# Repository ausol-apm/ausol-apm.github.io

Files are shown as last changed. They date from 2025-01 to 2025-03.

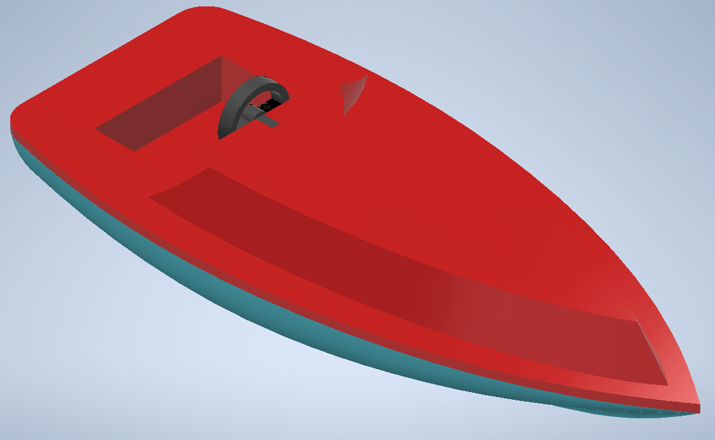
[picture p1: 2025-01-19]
Design and simulation/Inventor/Modelado juguetes/Imagenes juguetes/Barco.png

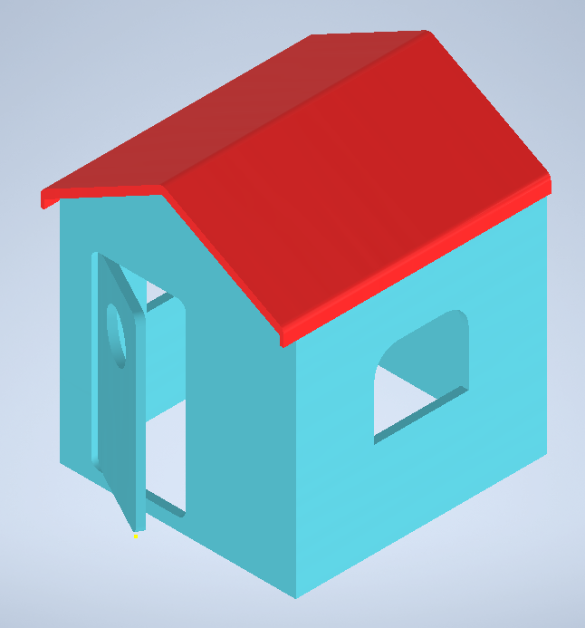
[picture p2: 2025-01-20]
Design and simulation/Inventor/Modelado juguetes/Imagenes juguetes/Casa.png

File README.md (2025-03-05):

**AUTOMATION SOLUTIONS - AUSOL**  
Propuesta de automatización de linea de producción de 3 juguetes, para la empresa _Bricajo Toys_.

**Integrantes**  
- Yovany Esneider Vargas Gutierrez
- Brian Enrique Muñoz Garcia
- Joyner Stiven Caballero Abril
- Camilo Andres Apraez Zamora

Se optó por montar la página web en Google Sites, para acceder a ella dirigirse a [Ausol Site](https://sites.google.com/unal.edu.co/ausol-automation-solutions).  
El video resumen se encuentra en la plataforma de YouTube [Video Resumen](https://youtu.be/QcR64jWf5vM).

*Automatización de Procesos de Manufactura  
Universidad Nacional de Colombia  
Sede Bogotá  
2024-2S*

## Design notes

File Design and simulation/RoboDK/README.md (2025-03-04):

Debido a inconvenientes con el tamaño del archivo .rdk, no fue posible subirlo directamente al GitHub. Por esta razón, se proporciona un enlace de Google Drive para su descarga.
https://drive.google.com/file/d/1TmyBnXiAjbIdtEMR1A-sOKN9FEcNRLlI/view?usp=sharing

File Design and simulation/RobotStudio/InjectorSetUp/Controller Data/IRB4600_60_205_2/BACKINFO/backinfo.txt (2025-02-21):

>>SYSTEM_ID:
VIRTUAL_USE

>>PRODUCTS_ID:
RobotWare Version: 6.15.08.00

  RobotWare Base
  English
  Drive System IRB 460/640/660/760/4600/66xx/6700
  ADU-790A in position X3
  ADU-790A in position Y3
  ADU-790A in position Z3
  Axis Calibration
  IRB 4600-60/2.05 Type C

>>HOME:
All public files and directories

>>SYSPAR:
SYS.cfg
PROC.cfg
MMC.cfg
EIO.cfg
SIO.cfg
MOC.cfg

>>TASK1: (T_ROB1,,)
SYSMOD\user.sys @ 
PROGMOD\Module1.mod @ 
PROGMOD\CalibData.mod @ 

>>EOF:

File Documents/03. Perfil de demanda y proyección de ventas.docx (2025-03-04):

Evaluación Financiera de la empresa de fabricación de juguetes Bricajo Toys aplicada la automatización por parte de Automation Solutions (AutoSol)

Tendencias del mercado de juguetes en Colombia:

- Crecimiento del mercado: El mercado colombiano de juguetes está valorado en aproximadamente $800.000 millones de pesos anuales y ha mostrado un crecimiento constante en los últimos años.
- Preferencias de los consumidores: Existe una creciente demanda de juguetes educativos y tecnológicos, así como de aquellos que promueven actividades al aire libre y el desarrollo de habilidades motoras.

Cifras que se basan en información consignada por la DIAN

“La industria de juguetes a nivel nacional se destaca en los últimos años, por su compromiso con la artesanía y la calidad. En Colombia, las ventas de juguetes alcanzan más de $ 800.000 millones al año y es uno de los negocios que continúa registrando crecimientos importantes, pues en los últimos 3 años se estima que esta categoría de juguetes ha incrementado un 10% su comercialización.”

Por lo tanto se estima un crecimiento del 3.33% anual, lo que implica que para el año 2025 habrá un crecimiento del 6.67%, 1,33 Billones de pesos colombianos aproximadamente.

Dado que no contamos con datos específicos de ventas mensuales para los juguetes mencionados, y basándonos en la información disponible, podríamos suponer que estos juguetes representan una categoría dentro del mercado total. Si asumimos que los juguetes de Barco, Casa y Moto constituyen aproximadamente el 5% del mercado total, estaríamos hablando de ventas anuales alrededor de $42.667 millones de pesos colombianos para el año 2025.

Consideraciones:

- Diciembre es el mes con mayor demanda debido a la Navidad.
- Abril muestra un aumento moderado por el Día del Niño.
- Junio y Julio tienen un ligero incremento por las vacaciones escolares.
- Enero a Marzo y Mayo a Septiembre son meses de baja demanda.

Distribución Mensual de ventas estimada:

Diciembre: 30%

Abril: 12%

Junio - Julio: 20% (10% cada mes)

Octubre: 8%

Demás meses (7): 4.28 %

Distribución Mensual de ventas por tipo de juguete estimada:

Motos: 40%

Barcos: 35%

Casas: 25%

Precios unitarios de cada juguete (en pesos Colombianos)

(Se indagaron precios en tiendas como Pepe Ganga):

Motos: 10.000

Barcos: 12.000

Casas: 15.000

Producción mensual máxima de juguetes por tipo de la planta Automatizada (Por unidades)

Motos: 14.757

Barcos: 12.873

Casas: 9086

Estimación de unidades vendidas mes a mes en Colombia para el 2025:

Estimación ventas mensuales por tipo de juguete (Unidades)
Mes | Moto | Barco | Casa
Enero | 29257 | 21333 | 12190
Febrero | 29257 | 21333 | 12190
Marzo | 29257 | 21333 | 12190
Abril | 81920 | 59733 | 34133
Mayo | 29257 | 21333 | 12190
Junio | 68267 | 49778 | 28444
Julio | 68267 | 49778 | 28444
Agosto | 29257 | 21333 | 12190
Septiembre | 29257 | 21333 | 12190
Octubre | 54613 | 39822 | 22756
Noviembre | 29257 | 21333 | 12190
Diciembre | 204800 | 149333 | 85333

Estimación de las ventas mes a mes en Colombia para el 2025:

Estimación ventas mensuales por tipo de juguete (Millones COP)
Mes | Moto | Barco | Casa
Enero | 292.57 | 256.00 | 182.86
Febrero | 292.57 | 256.00 | 182.86
Marzo | 292.57 | 256.00 | 182.86
Abril | 819.20 | 716.80 | 512.00
Mayo | 292.57 | 256.00 | 182.86
Junio | 682.67 | 597.33 | 426.67
Julio | 682.67 | 597.33 | 426.67
Agosto | 292.57 | 256.00 | 182.86
Septiembre | 292.57 | 256.00 | 182.86
Octubre | 546.13 | 477.87 | 341.33
Noviembre | 292.57 | 256.00 | 182.86
Diciembre | 2048.00 | 1792.00 | 1280.00

Perfil de la estimación promedio de la demanda en unidades de juguetes (Barco, Moto y casa) en Colombia para el año 2025, discriminado por cada mes del año

Perfil de la estimación promedio de la demanda en COP de juguetes (Barco, Moto y casa) en Colombia para el año 2025, discriminado por cada mes del año

Dado que ya existen ciertas empresas con el mismo tipo de productos comercializados en Colombia, se busca abarcar el 20% de este mercado, es decir 3313 millones de pesos COP.

Producción proyectada mensual (sin almacenamiento) por tipo de juguete (Unidades)
Mes | Moto | Barco | Casa
Enero | 14629 | 10667 | 6095
Febrero | 14629 | 10667 | 6095
Marzo | 14629 | 10667 | 6095
Abril | 40960 | 29867 | 17067
Mayo | 14629 | 10667 | 6095
Junio | 34133 | 24889 | 14222
Julio | 34133 | 24889 | 14222
Agosto | 14629 | 10667 | 6095
Septiembre | 14629 | 10667 | 6095
Octubre | 27307 | 19911 | 11378
Noviembre | 14629 | 10667 | 6095
Diciembre | 102400 | 74667 | 42667

Esto es lo que se tendría que producir para cubrir la demanda de ese 50% mes a mes sin embargo la planta automatizada tiene un limité de producción mensual como ya se especifico más arriba. Por lo que se recurre al almacenamiento de productos en los meses justamente anteriores para que se cumpla la demanda en los meses pico. Quedá de la siguiente manera.

Producción proyectada mensual por tipo de juguete dada la producción máxima de la planta automatizada (Unidades)
Mes | Moto | Barco | Casa
Enero | 14629 | 10667 | 6095
Febrero | 14629 | 10667 | 6095
Marzo | 21669 | 10667 | 6095
Abril | 33920 | 29867 | 17067
Mayo | 14629 | 10667 | 6095
Junio | 34133 | 24889 | 14222
Julio | 34133 | 24889 | 14222
Agosto | 37912 | 10667 | 6095
Septiembre | 33920 | 27171 | 6095
Octubre | 33920 | 29580 | 18380
Noviembre | 33920 | 29580 | 20880
Diciembre | 33920 | 29580 | 20880

Estimación de la producción mensual dada la producción mensual máxima permitida por la planta automatizada para el año 2025:

Producción proyectada mensual por tipo de juguete dada la producción máxima de la planta automatizada (Millones COP)
Mes | Moto | Barco | Casa
Enero | 146 | 128 | 91
Febrero | 146 | 128 | 91
Marzo | 146 | 128 | 91
Abril | 410 | 358 | 256
Mayo | 146 | 128 | 91
Junio | 341 | 299 | 213
Julio | 341 | 299 | 213
Agosto | 146 | 128 | 91
Septiembre | 146 | 128 | 91
Octubre | 273 | 239 | 171
Noviembre | 146 | 128 | 91
Diciembre | 1024 | 896 | 640

Referencias bibliográficas

Redacción Economía. (2023, 13 de noviembre). Industria de juguetes mueve $0,8 billones al año. El Nuevo Siglo. https://www.elnuevosiglo.com.co/economia/industria-de-juguetes-mueve-08-billones-al-ano

Molina, J. (2012, 8 de diciembre). Negocio de los juguetes mueve $660.000 millones cada año. La República. https://www.larepublica.co/empresas/negocio-de-los-juguetes-mueve-660-000-millones-cada-ano-2027371

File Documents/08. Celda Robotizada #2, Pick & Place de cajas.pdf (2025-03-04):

# AUSOL - Setting-up de brazo robótico para aplicación de pick and place

Vargas Y., Caballero J., Muñoz B., and Apraez C.

yvargasgu@unal.edu.co, jocaballeroa@unal.edu.co, bmunozg@unal.edu.co, and capraezz@unal.edu.co

### 1. INTRODUCCION

La creciente demanda de eficiencia y competitividad en el sector industrial ha

impulsado la adopción de soluciones automatizadas que reduzcan los tiempos de ciclo,

mejoren la calidad del producto y, sobre todo, garanticen la seguridad de los operarios. En

este contexto, las celdas de trabajo con robots se han convertido en un elemento clave para

optimizar procesos repetitivos o con alto riesgo humano.

El presente documento se enfoca en la implementación de una celda robótica de

pick and place, diseñada para transferir cajas desde una banda transportadora hasta un área

de disposición (por ejemplo, un pallet o una estación de empaquetado). La propuesta gira

en torno al uso de un Motoman MH50, acompañado de sistemas de alimentación y

resguardo adecuado, con el fin de ejecutar las tareas de manipulación de manera segura y

consistente.

A lo largo de este texto, se describen los componentes fundamentales de la celda

(robot, controlador, elementos terminales, bandas transportadoras, etc.) y se abordan los

principales peligros y requisitos de seguridad, tomando como referencia la norma ISO

10218-1:2011. Asimismo, se presentan las estrategias de mitigación y el enfoque para la

evaluación de riesgos, con el objetivo de cumplir la normativa y garantizar un entorno de

trabajo seguro, productivo y alineado con las tendencias actuales de automatización.

### 2. ANALISIS:

La etapa del proceso seleccionada consiste en tomar las cajas que salen de la banda

transportadora (pick) y depositarlas en un punto de acopio (place), donde posteriormente un

carro de carga las recogerá para su siguiente fase de transporte o almacenamiento. En dicho

sentido, existen dos preguntas orientadoras para comprender el motivo de los cambios a realizar en la fase: primero (2.1) ¿por qué integrar un robot en este procedimiento?; y

segundo (2.2) ¿qué valor agregado otorga?

2.1. ¿POR QUÉ INTEGRAR UN ROBOT EN ESTE PROCEDIMIENTO?
2.1.1. Seguridad y Salud Ocupacional
2.1.1.1. Reducción del riesgo de lesiones

De acuerdo con la National Institute for Occupational Safety and Health (NIOSH), levantar

cargas superiores a 10 kg de forma repetitiva incrementa de manera significativa el riesgo

de trastornos musculoesqueléticos, especialmente en la región lumbar.

Estudios realizados por Waters et al. (1993) sugieren que la manipulación manual de cargas

por encima de los límites recomendados (10–15 kg según la frecuencia de levantamiento)

se asocia a una mayor incidencia de lesiones de espalda y ausentismo laboral.

Al introducir un robot capaz de manipular cajas de 12.5 kg, se elimina casi por completo la

necesidad de que los operarios realicen esfuerzos repetitivos, reduciendo el riesgo de

lesiones agudas y crónicas.

2.1.2. Ergonomía y Movimientos Repetitivos
2.1.2.1. Minimización de sobreesfuerzos humanos

Estudios ergonómicos como los basados en la Revised NIOSH Lifting Equation

recomiendan limitar el peso de la carga y la frecuencia de levantamiento para prevenir

lesiones.

Retirar la carga repetitiva de 12.5 kg al día (que fácilmente excede los límites de la

ecuación NIOSH según frecuencia) reduce factores de riesgo críticos como la flexión

repetitiva del tronco o la torsión de la columna.

2.1.2.2. Mejora del entorno de trabajo

Un informe de la International Federation of Robotics (IFR) indica que, en aplicaciones

logísticas, la automatización con robots disminuye entre un 50 % y un 70 % la necesidad de

manipulación manual de cargas.

Al reducir esfuerzos físicos, el personal puede focalizarse en labores de supervisión y

control de calidad, aumentando su productividad y satisfacción laboral.

2.2. ¿QUÉ VALOR AGREGADO OTORGA?
2.2.1. Eficiencia en la Cadena de Producción
2.2.1.1. Incremento de la productividad

Según datos de la IFR (2022), la instalación de robots en tareas de paletizado y

manipulación puede aumentar el throughput hasta en un 30 % en comparación con la

manipulación manual.

Otro estudio de McKinsey Global Institute destaca que la automatización de procesos

repetitivos puede liberar hasta un 20 % del tiempo total de producción para actividades de

mayor valor añadido.

2.2.1.2. Consistencia y reducción de errores

Robots programados con trayectorias y rutinas de agarre precisas reducen drásticamente la

variabilidad que es típica de la intervención humana; esto conlleva menos cajas mal

colocadas o dañadas.

Gultekin et al. (2013) demostraron que la asignación óptima de tareas al robot junto con

una correcta secuenciación de movimientos disminuye paradas imprevistas y eleva la

eficiencia global en celdas de dos máquinas.

2.2.1.3. Optimización del espacio

Al ubicar estratégicamente el robot entre la banda y los tres pallets, se minimizan

desplazamientos y tiempos muertos.

2.2.2. Rentabilidad y Retorno de la Inversión (ROI)
2.2.2.1. Disminución de costos laborales y de salud

OSHA (2019) reporta que los costos directos e indirectos asociados a lesiones laborales

(tratamientos médicos, ausencias, rotación de personal) suelen superar los USD 40 000 por

incidente en casos de problemas lumbares graves.

Implementar un robot reduce estos costos y ayuda a cumplir regulaciones de salud,

evitando potenciales multas o sanciones.

Amortización a corto o mediano plazo

Estudios recopilados por la RIA y la IFR sugieren que la adopción de celdas robóticas en

paletizado puede lograr un ROI entre 1 y 3 años, dependiendo del volumen de producción y

costos locales de mano de obra.

La posibilidad de operar 24/7 aumenta la producción anual y, por ende, acelera la

recuperación de la inversión.

### 3. SELECCIÓN DE COMPONENTES INICIALES Y RUTINA DE LA

CELDA:

3.1. Robot Motoman MH50 (Yaskawa)

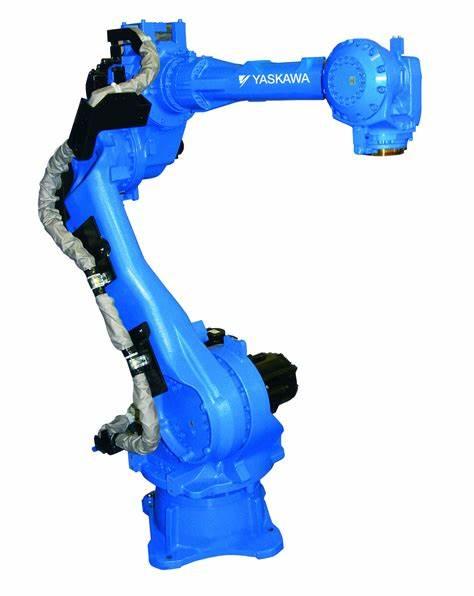
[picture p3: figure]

Figura 1. Motoman MH50. Fuente: adaptado de directindustry.de

Capacidad de carga de hasta 50 kg.

Adecuado para tareas de manipulación, paletizado o pick and place de cajas.

3.2. Controlador YRC1000 + Teach Pendant (Yaskawa)

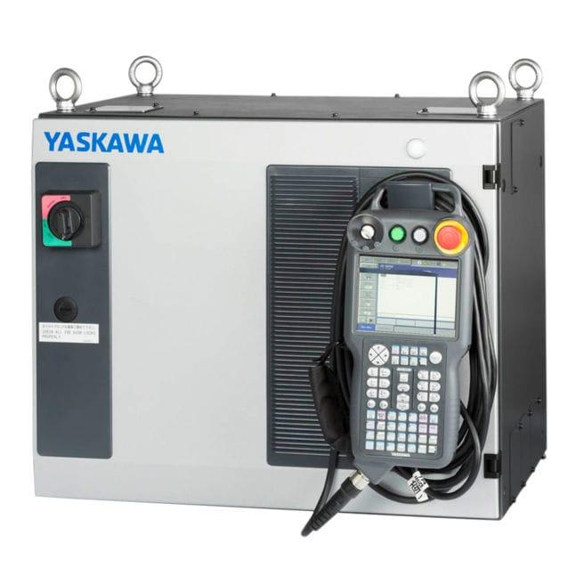
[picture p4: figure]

Figura 2. Controlador YRC1000. Fuente: adaptado de directindustry.de

Sistema de control dedicado al robot.

Incluye consola de programación para configurar trayectorias, velocidad y otras rutinas.

3.3. Gripper de vacío de 4 copas RobotiQ

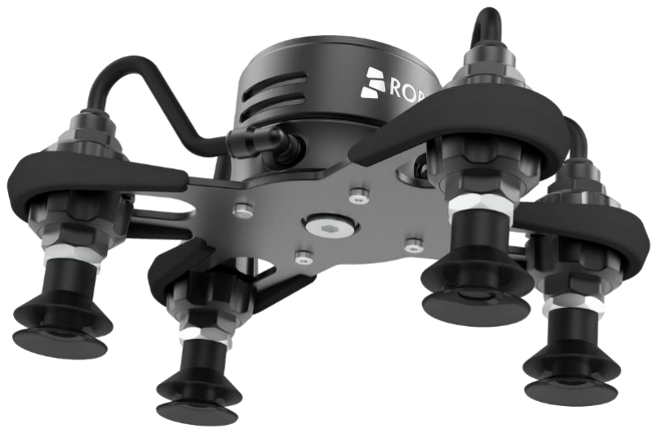
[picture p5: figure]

Figura 3. Gripper de vacío de 4 copas. Fuente: adaptado de RobotiQ.com

Herramienta de final de brazo (end effector) que utiliza succión para sujetar cajas.

Diseño modular que facilita la adaptación a distintas dimensiones de embalaje.

3.4. Banda transportadora de 3,5 m para cajas (ConveyorT)

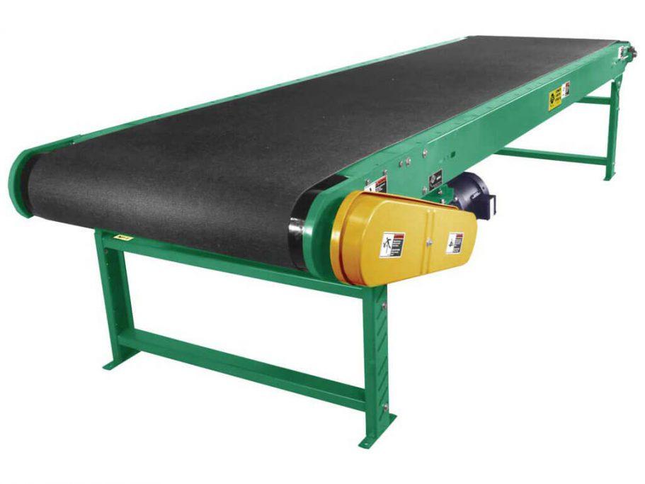
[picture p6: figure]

Figura 4. Banda transportadora. Fuente: adaptado de MercadoLibre.com

Medio de alimentación de las cajas hacia la zona de alcance del robot.

Posible motorización y control de velocidad para sincronizar con el ciclo del robot.

3.5. PLC S7-1200 (Siemens)

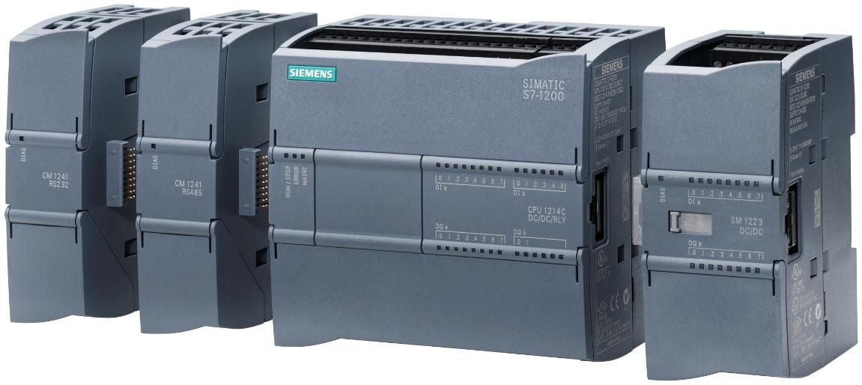
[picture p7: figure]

Figura 5. PLC S7-1200. Fuente: adaptado de Siemens

Controlador lógico programable que gestiona la automatización y permite la comunicación

entre sensores, robot y dispositivos periféricos.

3.6. Proceso diseño de celda:

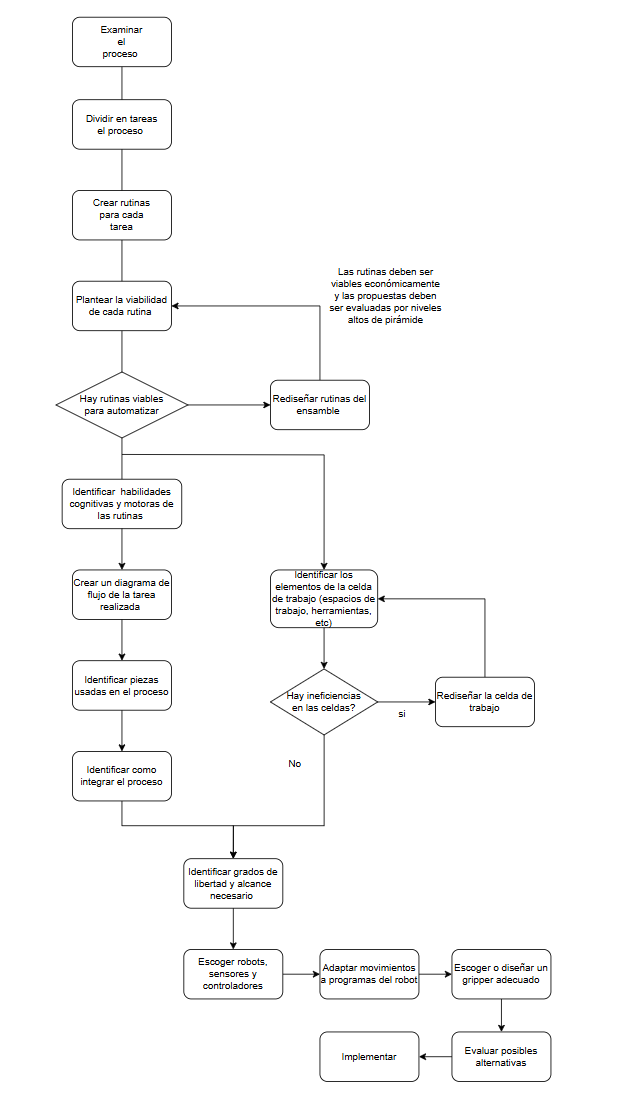
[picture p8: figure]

Figura 6. Diagrama diseño de celda.

3.7. Rutina de la celda:

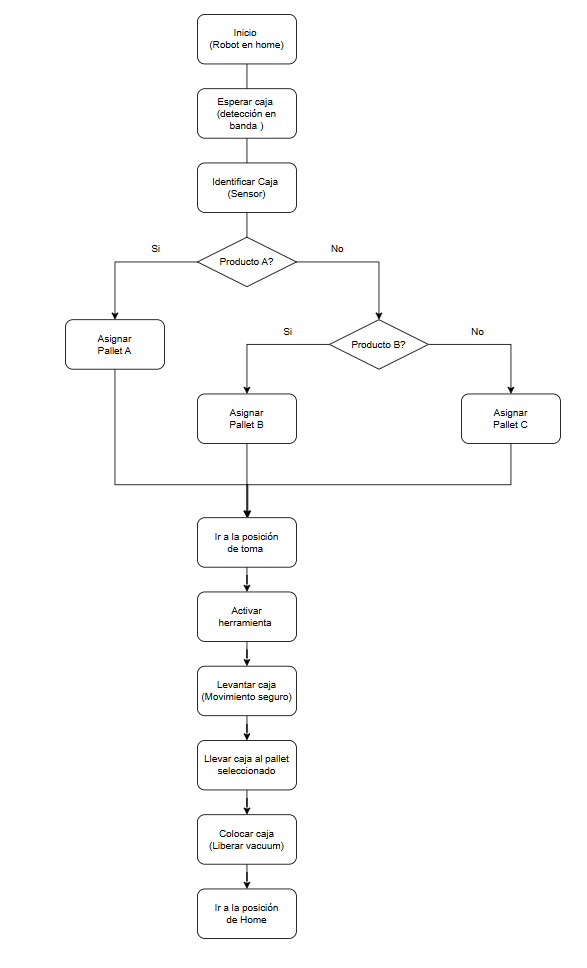
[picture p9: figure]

Figura 7. Diagrama rutina de la celda.

3.8. Duty cicle y throughput:

En simulación, la celda robotizada realiza un ciclo de trabajo en 3 segundos, dicho ciclo

consiste en tomar la caja desde la banda transportadora y luego dejarla en el pallet para

finalmente volver a una posición de home.

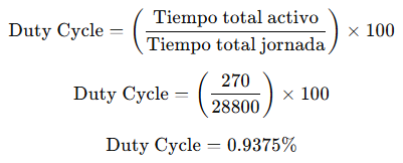
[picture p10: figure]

### 4. IDENTIFICACIÓN DE PELIGROS:

4.1. Movimientos imprevistos o fuera de control del robot.

Causa: Fallo en el sistema de control, interferencias electromagnéticas o averías en

componentes mecánicos que llevan a desplazamientos inesperados.

Consecuencia: Aplastamiento, impacto o cizallamiento de personas en la zona.

4.2. Atrapamiento entre partes móviles del robot y estructuras fijas.

Causa: Espacio reducido en la trayectoria del robot, falta de resguardos o falta de parada de

emergencia.

Consecuencia: Posibles lesiones graves (aplastamiento, cizallamiento).

4.3. Liberación imprevista de energía acumulada (neumática, hidráulica o

gravedad).

Causa: Fallo de componentes que mantienen presiones internas, pérdida de potencia que

libera frenos o contrapesos sin control.

Consecuencia: Golpes, impactos o eyección de piezas/elementos a alta velocidad.

4.4. Fallo en el elemento terminal (pinza o herramienta) y desprendimiento de

carga.

Causa: Sujeción deficiente de la herramienta o de la pieza, sobrecarga de la pinza, fatiga de

materiales.

Consecuencia: Caída o expulsión de la pieza de trabajo, con riesgo de impactos o golpes.

4.5. Peligros eléctricos en los componentes del robot y de las bandas

transportadoras.

Causa: Contacto con conexiones o componentes en tensión, falta de toma de tierra,

aislamientos en mal estado.

Consecuencia: Choque eléctrico, quemaduras y potencial efecto sobre marcapasos.

4.6. Interferencias electromagnéticas y fallos en la comunicación entre

dispositivos

Causa: Sobrecargas o fallos en la red de comunicación industrial (Profinet, Ethernet/IP,

etc.).

Consecuencia: Errores en la activación de paradas de emergencia o fallos en los

enclavamientos de seguridad.

4.7. Posible proyección o expulsión de piezas desde las bandas transportadoras.

Causa: Golpes del robot al manipular cajas, fallos en los sensores que posicionan la

mercancía, bloqueo de la cinta.

Consecuencia: Impactos en el personal en las cercanías o daños a equipamiento.

4.8. Peligros ergonómicos al programar o hacer mantenimiento dentro de la

celda.

Causa: Consola de guiado mal diseñada, posturas forzadas en la zona de acceso, ubicación

inadecuada de botones de parada o validación.

Consecuencia: Fatiga, lesiones musculoesqueléticas, retraso en la reacción ante una

emergencia.

4.9. Inicio inesperado tras reanudación de potencia.

Causa: Falta de secuencia de arranque seguro, modos manuales/automático mal diseñados,

restablecimiento no controlado tras un paro o corte de energía.

Consecuencia: Arranque del robot o la cinta sin previo aviso, atrapamiento o golpe a los

operarios.

4.10. Fallo o desconexión de sistemas de seguridad o dispositivos de

enclavamiento.

Causa: Interruptores mal instalados, ausencia de mantenimiento preventivo, manipulación

voluntaria de resguardos.

Consecuencia: Acceso no controlado a la zona de movimiento del robot y riesgo de

colisiones.

### 5. ANÁLISIS DE RIESGO ASOCIADO:

La norma ISO 12100 establece que cada organización puede adaptar la escala y

clasificación de los parámetros de riesgo, siempre y cuando se justifique con criterios de

experiencia, datos estadísticos o consenso de expertos (ISO 12100, secciones sobre

evaluación de riesgos). Además, la ISO 13849-1 sugiere considerar frecuencias de acceso,

facilidad de detección de fallos y severidad del daño para estimar cuán “peligrosa” es una

situación y qué nivel de seguridad deben cumplir los sistemas de mando.

Por tanto, las escalas de S, P, F y E aquí mostradas son un ejemplo respaldado por:

Criterios de severidad difundidos por los institutos de seguridad industrial y la

literatura técnica, que relacionan ciertos tipos de lesiones (leve, moderada, grave,

mortal) con valores 1 a 4.

Referencias históricas en la industria sobre cuán frecuente (F) y probable (P) puede

llegar a ser un accidente dada la experiencia en plantas con robots industriales.

Experiencia de campo (casos documentados) que reflejan cómo la posibilidad de

evitación (E) depende de la velocidad del robot, la presencia de resguardos, alarmas,

etc.

5.1. Escalas propuestas y justificación

Se propone la siguiente tabla de valores, derivada de los criterios más habituales en el

sector robótico (conforme a guías como HSE’s “Risk assessment of machinery” y la

práctica recogida en ISO/TR 14121-2).

5.1.1. Severidad (S)

La gravedad de las lesiones se clasifica en función del posible desenlace:

S = 1: Lesiones leves que no requieren baja laboral prolongada (p.ej. contusiones,

laceraciones pequeñas).

S = 2: Lesiones moderadas, recuperables, con cierta duración (p.ej. fracturas

simples, heridas que requieren sutura).

S = 3: Lesiones graves o permanentes (amputaciones, daños irreversibles en

extremidades, quemaduras de 3er grado).

S = 4: Lesiones muy graves que pueden conducir a la muerte o dejan secuelas muy

significativas (por ejemplo, traumatismo craneoencefálico severo).

5.1.2. Probabilidad de que ocurra el evento (P)

Este factor valora la probabilidad de que un peligro cause daño en caso de

exposición:

P = 1 (muy baja) Sucede cuando hay sistemas de seguridad muy fiables (IEC 61508

/ ISO 13849-1), una frecuencia de fallos muy reducida (<10⁻⁷/h), y el escenario

exige condiciones muy improbables.

P = 2 (baja) Se asume que, aunque la situación peligrosa existe, hay barreras o

controles que reducen de manera significativa la ocurrencia.

P = 3 (media) Sin ser común, existe una ocurrencia ocasional de fallos (p.ej. uno o

dos eventos al año en una planta con varios robots).

P = 4 (alta) Es el caso donde se presentan condiciones inestables o fallos frecuentes

(varios eventos por mes).

5.1.3. Frecuencia / Exposición (F)

Es la periodicidad con la que las personas se encuentran en o cerca del peligro:

F = 1 (exposición esporádica) Tareas puntuales (1 vez al mes o menos).

F = 2 (exposición ocasional) Accesos semanales o diarios muy breves a la zona

peligrosa.

F = 3 (exposición frecuente) Presencia habitual (varias veces al día) cerca del robot,

p.ej. para ajustar programas o supervisar la línea.

F = 4 (exposición continua) El operario permanece a menudo en la zona

(mantenimiento intensivo, trabajo cooperativo continuo).

5.1.4. Posibilidad de Evitación (E)

Valora qué tan fácil es que la persona pueda evitar o escapar de las consecuencias

cuando el peligro se activa:

E = 1 (muy alta) El operador ve venir el peligro con claridad y puede apartarse sin

riesgo (velocidad muy baja o aviso prolongado).

E = 2 (alta) Puede evitarse si el operador está atento, hay margen de reacción y

señales de alerta (luz, sonido).

E = 3 (media) A veces es posible evitarlo, pero no siempre (movimientos más

rápidos, visibilidad parcial).

E = 4 (baja) Difícil de esquivar: acción muy rápida, espacios confinados, o señales

de alerta insuficientes.

Estas consideraciones se recogen de la experiencia en robótica industrial: a mayor

velocidad y complejidad de movimientos, más difícil es reaccionar a tiempo (ISO 10218-1,

cap. 5.6 y 5.7, sobre velocidades reducidas y modos de operación).

5.2. Valoración HRN
5.2.1. Movimientos imprevistos o fuera de control (Peligro 1)

Severidad = 4: Un brazo robot de 50 kg de carga útil (Motoman MH50) puede

impactar con fuerza suficiente para lesiones fatales (cabeza, tórax).

Probabilidad = 2: Existe un riesgo de fallo en sistemas de control, pero su

probabilidad es baja cuando se siguen las directrices ISO 13849-1.

Frecuencia (F) = 3: El personal de mantenimiento/programación puede entrar varias

veces al día o por turnos en la celda.

Evitación (E) = 3: A velocidades normales (aceleraciones de 2-3 m/s²) puede ser

complejo reaccionar.

HRN = 4 × 2 × 3 × 3 = 72 (Riesgo alto)

5.2.2. Atrapamiento entre partes móviles y estructuras fijas (Peligro 2)

S = 3: Atrapamiento suele implicar aplastamiento o cizallamiento grave en

extremidades, con posibles amputaciones.

P = 3: Si no se respetan enclavamientos, o se anulan resguardos, es factible.

F = 3: La celda pick and place puede requerir ajustes/limpiezas diarias o semanales,

exponiendo a la persona con cierta regularidad.

E = 3: El espacio de trabajo a menudo es reducido; la reacción puede ser tardía si el

robot inicia un ciclo en automático.

HRN = 3 × 3 × 3 × 3 = 81 (Riesgo alto)

5.2.3. Liberación imprevista de energía acumulada (Peligro 3)

S = 3 Un desplome del brazo por pérdida de potencia del freno o la salida violenta

de aire/hidráulico puede ocasionar lesiones graves.

P = 2 Con un buen mantenimiento preventivo, no suele ocurrir a menudo.

F = 2 El acceso para mantenimiento del circuito hidráulico/neumático no es

continuo, sino ocasional.

E = 2 Una vez se liberó la energía, la persona tiene cierto margen para alejarse,

siempre que siga procedimientos.

HRN = 3 × 2 × 2 × 2 = 24 (Riesgo medio)

5.2.4. Fallo en el elemento terminal y desprendimiento de carga (Peligro 4)

S = 3 Un objeto de varios kilos cayendo puede provocar fracturas o traumatismos.

P = 3 Errores de sujeción (fuerza de la pinza, detección de pieza) pueden ser

relativamente comunes si no se calibran bien sensores.

F = 2 El operario no suele colocarse directamente bajo la pieza, pero sí puede

ocurrir durante inspecciones.

E = 3 Es factible evitar estar debajo de la carga, pero a veces el operario desconoce

que la pinza está fallando.

HRN = 3 × 3 × 2 × 3 = 54 (Medio-alto)

5.2.5. Peligros eléctricos (Peligro 5)

S = 4 Una descarga de alta tensión (brazos robóticos grandes suelen emplear 400-

480 V trifásicos) puede ocasionar paro cardiorrespiratorio.

Según el IEC 60204-1 (sistemas eléctricos en máquinas); tensiones altas implican

riesgo letal.

P = 2 Con instalaciones correctas, la probabilidad de descarga se mantiene baja,

pero no es nula (posibles averías de aislamientos).

F = 2 El personal no accede rutinariamente a armarios eléctricos, pero hay

revisiones periódicas.

E = 2 Puede haber avisos y EPI, pero un contacto accidental con cables sin

protección se produce sin tiempo de reacción.

HRN = 4 × 2 × 2 × 2 = 32 (Medio)

5.2.6. Interferencias electromagnéticas y fallos en la comunicación entre

dispositivos (Peligro 6)

S = 3 Un fallo en la comunicación puede provocar movimientos erráticos.

P = 2 Las interferencias electromagnéticas pueden ocurrir en entornos industriales

con alto ruido eléctrico, pero si la instalación sigue normas como IEC 60204-1, el

riesgo es menor.

F = 3 La celda robótica opera de forma continua, por lo que la exposición a fallos de

comunicación es frecuente.

E = 3 si la falla es repentina, puede ser difícil evitarla antes de que cause un

problema operativo.

HRN=3×2×3×3=54 (Medio-alto)

5.2.7. Proyección o expulsión de piezas (Peligro 7)

S = 2 Normalmente son cajas o paquetes con masa limitada, resultando en

contusiones o lesiones oculares.

P = 3 Atascos en bandas y errores de posicionamiento son relativamente frecuentes

(sobre todo en líneas rápidas).

F = 3 El operario suele estar cerca para supervisar el flujo y retirar obstrucciones.

E = 3 Puede haber alguna posibilidad de reacción, pero si la expulsión es súbita, el

operario podría no esquivarlo a tiempo.

HRN = 2 × 3 × 3 × 3 = 54 (Medio-alto)

5.2.8. Peligros ergonómicos (Peligro 8)

S = 2 Suele implicar lesiones musculoesqueléticas no mortales (tendinitis,

lumbalgias).

P = 2 Si no se diseña bien la consola o el acceso, la probabilidad de mala postura

repetitiva es moderada.

F = 3 El operario puede programar o vigilar la celda varias veces al día.

E = 2 Puede corregir postura, pero no siempre hay espacio ni hay conciencia

ergonómica suficiente.

HRN = 2 × 2× 3 × 2 = 24 (Bajo)

5.2.9. Inicio inesperado tras reanudación de potencia (Peligro 9)

S = 3 Si el robot se reinicia de forma brusca, puede impactar en el operario que está

dentro.

P = 1 Bien diseñado (ISO 10218-1 y IEC 60204-1), no debería moverse al

reconectar energía, pero hay fallos documentados.

F = 3 Cada vez que haya un corte de luz o mantenimiento, existe exposición.

E = 3 El operario podría oír el arranque, pero la reacción puede no ser inmediata.

HRN = 3 × 1 × 3 × 3 = 27 (Medio)

5.2.10. Fallo o desconexión de sistemas de seguridad (Peligro 10)

S = 4 Si fallan enclavamientos/ barreras, el robot queda libre de iniciar movimiento

sin protección.

P = 2 En un sistema con verificaciones y autodiagnóstico, es poco probable, pero

puede suceder por manipulación dolosa o averías.

F = 2 El fallo puede ocurrir en cualquier momento, pero la detección puede ser

tardía.

E = 3 El operario no sabrá que el resguardo está inoperativo hasta que se produzca

una maniobra peligrosa; difícil de evitar.

HRN = 4 × 2 × 2 × 3 = 48 (Medio-alto)

### 6. COMPONENTES DE SEGURIDAD:

6.1. Movimientos imprevistos o fuera de control (Peligro 1)
- Requiere componentes de seguridad:

Sí. Se necesitan sistemas de paro de emergencia, funciones de paro de

seguridad, interbloqueos que corten la potencia de accionamiento del robot

ante la apertura de protecciones, y sistemas de control redundantes para

minimizar la probabilidad de un movimiento inesperado.

Deben aplicarse medidas de ingeniería: resguardos perimetrales, control de

velocidad reducida y dispositivos de validación.

- Medidas complementarias (manuales/EPP):

Formación específica para evitar acceso indebido a la zona de riesgo,

procedimientos de consignación (lock-out/tag-out), y uso de EPP, por

ejemplo, calzado de seguridad.

No obstante, debido a la alta severidad, el componente de seguridad es

indispensable.

6.2. Atrapamiento entre partes móviles del robot y estructuras fijas (Peligro 2)
- Requiere componentes de seguridad:

Sí. El atrapamiento es uno de los peligros mecánicos más críticos. La ISO

10218-1 exige resguardos, dispositivos de limitación de ejes, sistemas de

enclavamiento y paros de seguridad.

Para celdas pick and place suelen utilizarse vallas de seguridad y finales de

carrera o sensores de posición que, unidos al control de seguridad, impidan

la colisión con postes, paredes o estructuras.

- Medidas complementarias:

Procedimientos claros para entrar en la celda, formación en detección de

zonas de aplastamiento, avisos visuales en puntos de posible atrapamiento.

Aunque las directrices y la formación ayudan, los resguardos físicos e

interbloqueos son obligatorios por el riesgo grave.

6.3. Liberación imprevista de energía acumulada (Peligro 3)
- Requiere componentes de seguridad:

La norma destaca la importancia de controlar la energía almacenada; no

obstante, esto se puede hacer mediante medidas complementarias.

- Medidas complementarias:

Manuales de procedimiento de “descarga de energía” antes de

mantenimiento, entrenamiento en lock-out/tag-out, y EPP apropiados

(guantes resistentes, etc.).

6.4. Fallo en el elemento terminal y desprendimiento de carga (Peligro 4)
- Requiere componentes de seguridad:

En muchos casos, se instalan sensores de agarre o sistemas de detección de

presión para verificar que la carga esté bien sujeta. No siempre se consideran

“componentes de seguridad” en el sentido estricto (no todos tienen categoría

de seguridad), pero sí pueden reducir la probabilidad de caída.

- Medidas complementarias:

Procedimientos de inspección diaria de las pinzas, formación en límites de

carga, y evitar que el operario permanezca bajo la pieza.

En muchas plantas se recurre a buenos manuales y entrenamiento como

medidas principales.

6.5. Peligros eléctricos en el robot y bandas transportadoras (Peligro 5)
- Requiere componentes de seguridad:

Sí. Cumplir con IEC 60204-1 (material eléctrico de máquinas), buena puesta

a tierra, dispositivos diferenciales, seccionadores con bloqueo, etc.

Se consideran “componentes de seguridad” los dispositivos de desconexión

que impiden energizar la máquina mientras se trabaja en ella.

- Medidas complementarias:

Procedimientos de lock-out/tag-out, manuales de uso que prohíban acceso a

partes en tensión, capacitación del personal que manipula cuadros eléctricos.

El EPP (guantes aislantes) se utiliza a veces, pero la clave es tener los

equipos eléctricos seguros en primer lugar.

### 6.6. Interferencias electromagnéticas y fallos en la comunicación entre dispositivos (Peligro 6)

- Requiere componentes de seguridad:

Uso de cables blindados y filtrado EMI para minimizar el ruido

electromagnético en líneas de señal.

Implementación de redundancia en comunicación (doble canal en redes

Profinet/Ethernet) para evitar la pérdida de datos

Aislamiento de señales de potencia y control, siguiendo normativas como

IEC 60204-1, para reducir interferencias eléctricas que puedan afectar los

sistemas de comunicación.

- Medidas complementarias:

Protocolos para reconfiguración segura del sistema en caso de pérdida de

comunicación.

Revisión periódica de conexiones, integridad de cables y correcto

enrutamiento de señales.

6.7. Proyección o expulsión de piezas desde las bandas transportadoras (Peligro 7)
- Requiere componentes de seguridad:

Se pueden instalar protectores o carenados sobre la cinta, barreras físicas o

“cortinas” de material resistente para que, si sale proyectada una caja, no

golpee a los operadores.

Según la evaluación de riesgos, a veces basta con resguardos parciales en las

zonas de transferencia entre robot y banda.

- Medidas complementarias:

Formación para no asomar partes del cuerpo en la banda en marcha,

procedimientos de parada antes de retirar atascos.

Por lo general, manuales de operación y entrenamiento son fundamentales,

pero una protección física (pantalla, barrera) suele ser muy recomendable.

6.8. Peligros ergonómicos (programación, posturas forzadas) (Peligro 8)
- Requiere componentes de seguridad:

Este tipo de riesgo rara vez se mitiga con “dispositivos de seguridad” en

sentido estricto (no hay un enclavamiento contra la mala postura).

- Medidas complementarias:

Formación ergonómica (posiciones de trabajo seguras, pausas de descanso),

manuales de buenas prácticas.

Dotar al operario de EPP adecuados (calzado, fajas si aplica), y asegurar

accesos a alturas correctas.

6.9. Inicio inesperado tras reanudación de potencia (Peligro 9)
- Requiere componentes de seguridad:

La ISO 10218-1 insiste en que la vuelta de la potencia no genere

movimientos automáticos sin una acción deliberada, lo que se logra con

componentes de control de seguridad (por ejemplo, circuitos que exijan

rearme manual tras un paro).

Sistemas de enclavamiento y control que impidan arranques accidentales y

garanticen la detención al reactivar la energía (IEC 60204-1, dispositivos de

seguridad redundantes).

- Medidas complementarias:

Procedimientos de puesta en marcha (checklists, verificación del área

despejada).

Avisos luminosos y sonoros antes de arrancar.

6.10. Fallo o desconexión de sistemas de seguridad (Peligro 10)
- Requiere componentes de seguridad:

Precisamente se trata de una falla de esos componentes. Para minimizarlo, la

ISO 10218-1 exige sistemas de control con autodiagnóstico y redundancia

(PL d o SIL 2). Se emplean circuitos a prueba de fallos que, ante el menor

error, detienen el robot.

También se necesitan sellos o candados en los resguardos para evitar

desconexiones voluntarias.

- Medidas complementarias:

Un plan de mantenimiento y auditoría de seguridad, manuales que prohíban

manipular los enclavamientos.

Entrenamiento para detectar avisos de fallo en el sistema de control y

reportar inmediatamente.

### 7. CONCLUSIONES EN LAS MEDIDAS DE SEGURIDAD:

Peligros que requieren siempre componentes de seguridad:

- Movimientos imprevistos, atrapamiento, peligros eléctricos, reanudación de

potencia inesperada y fallo de sistemas de seguridad son ejemplos claros donde la

ISO 10218-1 y la ISO 12100 indican que la solución principal debe ser de tipo

ingeniería y control de seguridad (enclavamientos, circuitos redundantes, resguardos

físicos, etc.).

Peligros que pueden mitigarse principalmente con manuales de uso, entrenamiento y/o

EPP:

- Peligros ergonómicos (8) dependen sobre todo del diseño ergonómico y la

formación, no tanto de un “interlock”.

- Proyección de piezas (7) puede requerir pantallas de protección sencillas, pero

buena parte del control recae en procedimientos (parar la banda antes de intervenir)

y entrenamiento para no situarse en trayectorias peligrosas.

- Fallo en el elemento terminal (4) se atenúa con sensores y rutinas de mantenimiento,

pero muchas empresas refuerzan la prevención con procedimientos (verificar

sujeción, no colocarse debajo de la carga).

7.1. Componentes de seguridad elegidos:

Instalación de 3 cortinas de luz en los puntos de interacción con la banda

transportadora:

Aunque la ISO 10218-1 no menciona explícitamente los peligros asociados a las bandas

transportadoras en celdas robóticas, sí enfatiza la necesidad de identificar y mitigar los

riesgos derivados de los movimientos del robot y su interacción con el entorno. La omisión

de las bandas transportadoras en esta normativa no implica que no constituyan un peligro,

sino que su regulación debe abordarse bajo otras normativas y mejores prácticas de

seguridad industrial.

Por estas razones, el análisis de este riesgo no se incluyó en la Sección 4; sin embargo, en la

presente sección se desarrolla un estudio de los peligros asociados a las bandas

transportadoras dentro de una celda robótica, así como las medidas de seguridad

seleccionada.

Identificación de Peligros en Bandas Transportadoras:

Las bandas transportadoras, al operar en conjunto con sistemas robóticos, pueden

representar diversos riesgos para los operarios y el equipo, entre los que destacan:

- Atrapamiento de extremidades o ropa en el mecanismo de arrastre.
- Acceso involuntario de operarios a la zona de riesgo durante el funcionamiento.

Para garantizar un entorno seguro, se recomienda la instalación de cortinas de luz tipo 4

(ISO 13855) en las siguientes áreas de la celda robótica:

1. Zonas de interacción entre el robot y la banda transportadora, evitando el acceso del

operario mientras el sistema está en funcionamiento.

2. Áreas de carga y descarga manual, deteniendo el movimiento de la banda si una

persona ingresa a la zona de peligro.

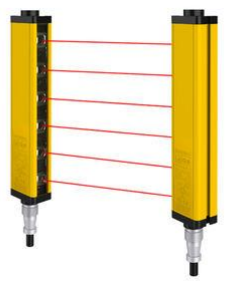
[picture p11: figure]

Figura 8. Cortina de luz de seguridad. Fuente: adaptado de directindustry.de

15,4 metros de reja de 2 metros de altura:

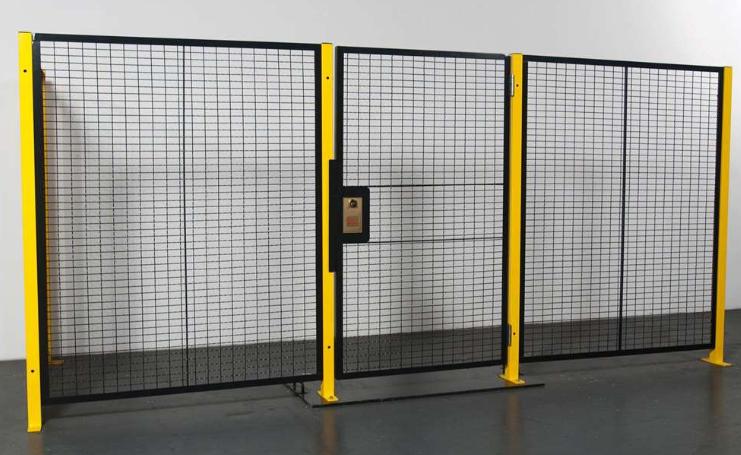
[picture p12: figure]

Figura 9. Rejas de seguridad. Fuente: adaptado de amhboston.com

Cumple con la ISO 13857, que establece que los resguardos físicos deben impedir el acceso

a la zona de peligro, considerando las dimensiones del robot y la posible extensión de sus

ejes.

Una altura de 2 metros asegura que un operario no pueda ingresar fácilmente por encima de

la estructura.

La reja evita el acceso involuntario y garantiza que solo el personal autorizado ingrese por

la puerta controlada.

Dos botones de parada de emergencia (uno dentro y otro fuera de la celda)

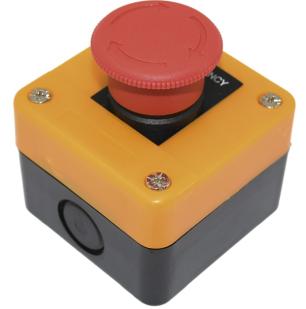
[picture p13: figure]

Figura 10. Botón de parada de emergencia. Fuente: adaptado de implmentos.cl

Cumple con la ISO 13850, que exige que los botones de parada de emergencia sean

accesibles y visibles en zonas estratégicas.

Botón exterior: Permite detener el sistema antes de ingresar a la celda, previniendo que

alguien acceda cuando el robot está en movimiento.

Botón interior: Asegura que, si un operario ya está dentro, tenga una forma rápida de

detener la operación en caso de emergencia.

Ambos están integrados en el circuito de seguridad, garantizando que una activación corte

la energía de manera inmediata.

Botón de hombre muerto

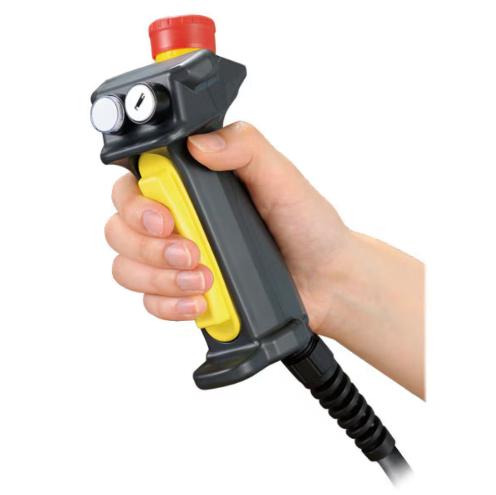
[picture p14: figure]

Figura 11. Botón de hombre muerto. Fuente: adaptado de us.idec.com

Según la ISO 10218-1, los robots industriales en modo de programación o mantenimiento

deben contar con dispositivos de validación, como un botón de hombre muerto en el teach

pendant.

Este botón asegura que, si el operador suelta la presión (por accidente o por emergencia), el

sistema se detiene automáticamente.

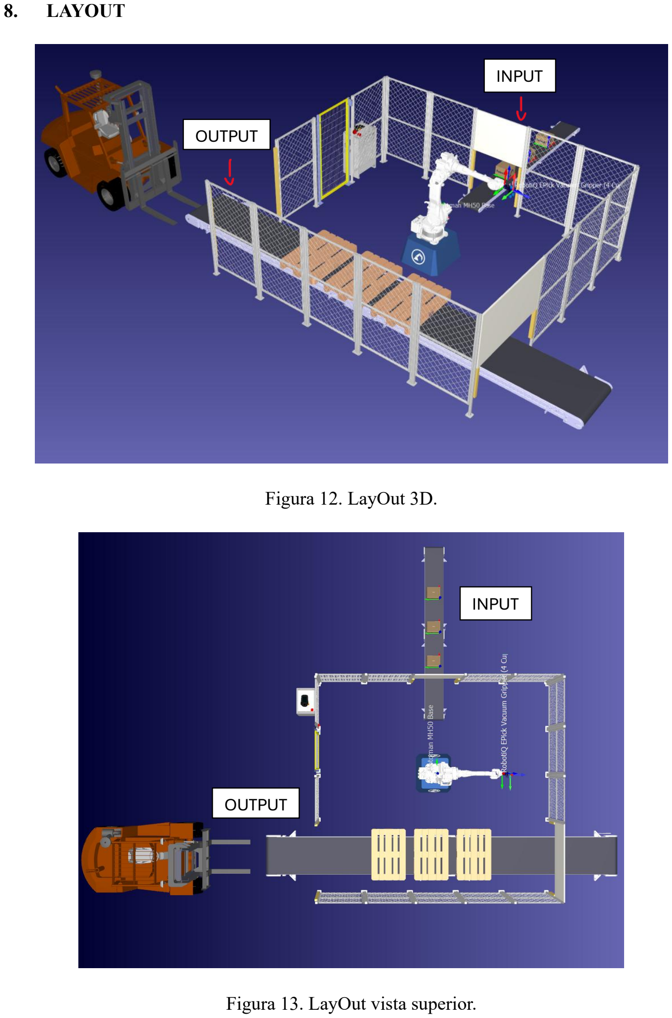
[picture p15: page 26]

### 8. LAYOUT

Figura 12. LayOut 3D.

Figura 13. LayOut vista superior.

### INPUT

### OUTPUT

### INPUT

### OUTPUT

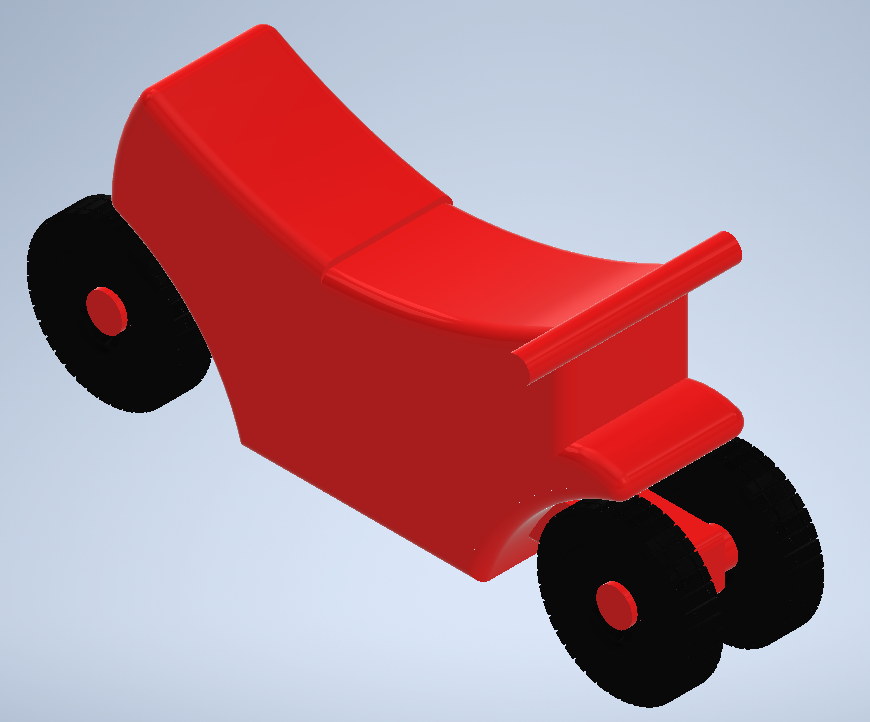
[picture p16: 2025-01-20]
Design and simulation/Inventor/Modelado juguetes/Imagenes juguetes/Moto.png

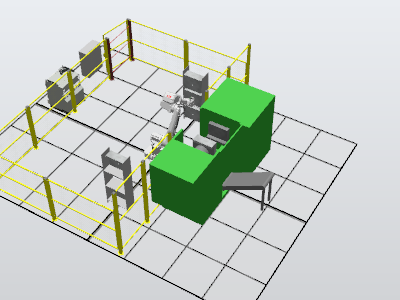
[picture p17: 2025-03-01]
Design and simulation/RobotStudio/InjectorSetUp/Station/Preview.png

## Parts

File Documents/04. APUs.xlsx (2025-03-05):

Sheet: Consolidado
API-1 | APU-2 | APU-3 | APU-4 | APU-5 | APU-6 | APU-7 | APU-8 | APU-9 | APU-10 | APU-11
$492349240.00 | $285949240.00 | $2977772.14 | $2854315.00 | $3511212.14 | $2596315.00 | $2621315.00 | $2543655.00 | $2468655.00 | $67022860.00 | $86988427.00
Consolidado | $951883006.28

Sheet: APU-1
FORMATO DE APU
CONTRATISTA: | BRICAJO TOYS
NIT:
PROYECTO: | Automatizacion planta producción de juguetes
LOCALIZACIÓN: | Bogota - Colombia
ACTIVIDAD A COTIZAR: | Celda Robotica de Paletizado
ITEM | 1
DESCRIPCION DEL ITEM | Celda robotizada 1
UNIDAD | UNIDAD
1 - EQUIPO
DESCRIPCIÓN DETALLADA | MARCA | UNIDAD | RENDIMIENTO | TARIFA | VR. UNITARIO
Pulidora 4 1/2 pulgadas | Dewalt | UNIDAD | 15 | $12000 | $180000.00
Planta electrica | DeWalt | UNIDAD | 15 | $12500 | $187500.00
Multimetro osciloscopio | Generico | UNIDAD | 15 | $3500 | $52500.00
Pulidora 7" | DeWalt | UNIDAD | 15 | $13500 | $202500.00
Taladro rotomartillo | DeWalt | UNIDAD | 15 | $4200 | $63000.00
Equipo de soldadura SMAW | Generico | UNIDAD | 15 | $35000 | $525000.00
Pistola de pintura | Corneta | UNIDAD | 15 | $2500 | $37500.00
kit tintas penetrantes | Magnaflux | UNIDAD | 15 | $1100 | $16500.00
kit espesor de pinturas | Dewalt | UNIDAD | 15 | $500 | $7500.00
SUB-TOTAL |  |  |  |  | $1272000.00
2 - MATERIALES
DESCRIPCIÓN | MARCA | UNIDAD | CANTIDAD | PRECIO UNIT | VR. UNITARIO
Cableado de control (UTP, 24V, etc.) | Varios | ML | 150 | $2000 | $300000.00
ENGEL VICTORY VC 60 / 50 TECH PRO CON MODULO DE INYECCION PARA TRES MATERIALES | Engel | UNIDAD | 1 | $210950000 | $210950000.00
Protección frontal acrílica (pantallas en la inyectora) | Industria local | m2 | 2 | $220000 | $440000.00
Cable potencia (motor banda, robot) | Varios | ML | 80 | $3000 | $240000.00
Conectores industriales / borneras | Weidmüller | UNIDAD | 10 | $25000 | $250000.00
Perno anclaje 1/2" | Fixer | UNIDAD | 150 | $1350 | $202500.00
Kit E-Stop y pulsadores (arranque, paro) | Siemens | UNIDAD | 1 | $850000 | $850000.00
Lámina galvanizada (para bases) calibre 18 | Varios | UNIDAD | 2 | $150000 | $300000.00
Sistema de lubricación / engrasado | SKF | UNIDAD | 1 | $500000 | $500000.00
Perfilería (ángulo 1" x 3/16") | Colmena | UNIDAD | 1 | $1500000 | $1500000.00
Tornillería / fijaciones | Fixer | UNIDAD | 4 | $250 | $1000.00
Pintura anticorrosiva 4 mils | Varios | Galon | 0.5 | $75000 | $37500.00
Adhesivo metro lineal | varios | m2 | 2 | $35000 | $70000.00
Tubo cuadrado 50x50x2 | colmena | UNIDAD | 5 | $156000 | $780000.00
Angulo 1" x 3/16 | Colmena | UNIDAD | 0.8 | $45300 | $36240.00
Golpe dobles | varios | UNIDAD | 2 | $1500 | $3000.00
Platinas | Varios | UNIDAD | 2 | $3500 | $7000.00
Robot IIRB 4600 | ABB | UNIDAD | 1 | $136570000 | $136570000.00
Gabinete de control y panel HMI (monitor+PC industrial) IRC5 | Advantech | UNIDAD | 1 | $6000000 | $6000000.00
End Effector para manipulación de moldes | Schunk | UNIDAD | 1 | $8500000 | $8500000.00
Fuente de poder / UPS industrial (3KVA) | Eaton | UNIDAD | 1 | $4800000 | $4800000.00
Barrera de seguridad / vallado modular | Troax | UNIDAD | 1 | $8000000 | $8000000.00
Cortina de 3 lineas | CGOLDENWALL Safety Light | UNIDAD | 1 | $2400000 | $2400000.00
Barrera de seguridad / vallado modular | Troax | UNIDAD | 1 | $9000000 | $9000000.00
SUB-TOTAL |  |  |  |  | $391737240.00
3 - TRANSPORTE
MATERIAL |  | UNIDAD | M3 ó Vol/Km | TARIFA | VR.UNITARIO
Flete marítimo inyectora (Europa - Buenaventura) |  | UNIDAD | 1 | $14000000 | $14000000.00
Flete aéreo robot (Europa - Bogota) |  | UNIDAD | 1 | $8000000 | $8000000.00
Transporte interno a la planta (camión grúa, etc.) |  | UNIDAD | 1 | $2000000 | $2000000.00
Seguro y nacionalización (inyectora + robot) |  | UNIDAD | 2 | $3000000.00 | $6000000.00
SUB-TOTAL |  |  |  |  | $30000000.00
4 - MANO DE OBRA
CUADRILLA |  | UNIDAD | RENDIMIENTO | VR. HH | VR. UNITARIO
Ingeniero mecatrónico senior (programación PLC + RobotStudio) |  | HH | 120 | $50000 | $6000000.00
Ingeniero mecánico (diseño y supervisión montaje moldes) |  | HH | 80 | $45000 | $3600000.00
Técnico electromecánico (conexiones, cableado, puesta en marcha) |  | HH | 200 | $28000 | $5600000.00
Ayudante de montaje |  | HH | 150 | $15000 | $2250000.00
SUB-TOTAL |  |  |  |  | $17450000.00
5 - SUBCONTRATADO
CUADRILLA |  | UNIDAD | RENDIMIENTO | PRECIO UNIT | VR. UNITARIO
Fabricación / Mecanizado CNC de moldes |  | UNIDAD | 6 | $5000000.00 | $30000000.00
Aluminio para Moldes (Aluminio 7075) |  | VOLUMEN CM3 | 379.35 | $15000.00 | $5690000.00
Proceso de CNC de moldes para la máquina |  | UNIDAD | 2 | $4000000.00 | $8000000.00
Calibración y ensayos de inyección |  | UNIDAD | 1 | $2500000.00 | $2500000.00
SUB-TOTAL |  |  |  |  | $46190000.00
6 - OTROS
ITEM |  | UNIDAD | RENDIMIENTO | PRECIO UNIT | VR. UNITARIO
Licencia RobotStudio |  | UNIDAD | 1 | $3200000.00 | $3200000.00
Capacitación al personal |  | UNIDAD | 1 | $2500000.00 | $2500000.00
SUB-TOTAL |  |  |  |  | $5700000.00
TOTAL COSTO DIRECTO |  |  |  |  | $492349240.00

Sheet: APU-2
FORMATO DE APU
CONTRATISTA: | BRICAJO TOYS
NIT:
PROYECTO: | Automatizacion planta producción de juguetes
LOCALIZACIÓN: | Bogota - Colombia
ACTIVIDAD A COTIZAR: | Celda Robotica de Paletizado
ITEM | 2
DESCRIPCION DEL ITEM | Celda robotizada 2
UNIDAD | UNIDAD
1 - EQUIPO
DESCRIPCIÓN DETALLADA | MARCA | UNIDAD | RENDIMIENTO | TARIFA | VR. UNITARIO
Multimetro osciloscopio | Generico | UNIDAD | 15 | $3500 | $52500.00
Pulidora 7" | DeWalt | UNIDAD | 15 | $13500 | $202500.00
kit espesor de pinturas | Dewalt | UNIDAD | 15 | $500 | $7500.00
Taladro rotomartillo | DeWalt | UNIDAD | 15 | $4200 | $63000.00
Equipo de soldadura SMAW | Generico | UNIDAD | 15 | $35000 | $525000.00
Pistola de pintura | Corneta | UNIDAD | 15 | $2500 | $37500.00
Pulidora 4 1/2 pulgadas | Dewalt | UNIDAD | 15 | $12000 | $180000.00
Planta electrica | DeWalt | UNIDAD | 15 | $12500 | $187500.00
kit tintas penetrantes | Magnaflux | UNIDAD | 15 | $1100 | $16500.00
Compresor de aire alta capacidad (para vacuum) | DeWalt | UNIDAD | 1 | $2500000 | $2500000.00
SUB-TOTAL |  |  |  |  | $3772000.00
2 - MATERIALES
DESCRIPCIÓN | MARCA | UNIDAD | CANTIDAD | PRECIO UNIT | VR. UNITARIO
Cableado de control (UTP, 24V, etc.) | Varios | ML | 150 | $2000 | $300000.00
Gripper de vacío 4 copas (EPick) | RobotiQ | UNIDAD | 1 | $12000000 | $12000000.00
Robot Motoman MH50 (carga máx. 50 kg) | Yaskawa | UNIDAD | 1 | $150000000 | $150000000.00
Cable potencia (motor banda, robot) | Varios | ML | 80 | $3000 | $240000.00
Controlador YRC1000 + Teach Pendant | Yaskawa | UNIDAD | 1 | $40000000 | $40000000.00
Conectores industriales / borneras | Weidmüller | UNIDAD | 10 | $25000 | $250000.00
Perno anclaje 1/2" | Fixer | UNIDAD | 150 | $1350 | $202500.00
Kit E-Stop y pulsadores (arranque, paro) | Siemens | UNIDAD | 1 | $850000 | $850000.00
Lámina galvanizada (para bases) calibre 18 | Varios | UNIDAD | 2 | $150000 | $300000.00
Malla eslabonada / paneles para cercado extra | Varios | m2 | 20 | $75000 | $1500000.00
Perfilería (ángulo 1" x 3/16") | Colmena | UNIDAD | 1 | $1500000 | $1500000.00
Banda transportadora 9 m para cajas | ConveyorT | UNIDAD | 1 | $18000000 | $18000000.00
PLC S7-1200 p/ automatización y comunic. | Siemens | UNIDAD | 1 | $1200000 | $1200000.00
HMI táctil 7" | Varios | UNIDAD | 1 | $2500000 | $2500000.00
Barrera de seguridad / vallado modular | Troax | UNIDAD | 1 | $8000000 | $8000000.00
Sensor fotoeléctrico p/ detección cajas | Omron | UNIDAD | 12 | $600000 | $1200000.00
Cortina de luz de seguridad | CGOLDENWALL Safety Light | UNIDAD | 3 | $2400000 | $7200000.00
Tornillería / fijaciones | Fixer | UNIDAD | 4 | $250 | $1000.00
Pintura anticorrosiva 4 mils | Varios | Galon | 0.5 | $75000 | $37500.00
Adhesivo metro lineal | varios | m2 | 2 | $35000 | $70000.00
Tubo cuadrado 50x50x2 | colmena | UNIDAD | 5 | $156000 | $780000.00
Angulo 1" x 3/16 | Colmena | UNIDAD | 0.8 | $45300 | $36240.00
Golpe dobles | varios | UNIDAD | 2 | $1500 | $3000.00
Platinas | Varios | UNIDAD | 2 | $3500 | $7000.00
SUB-TOTAL |  |  |  |  | $246177240.00
3 - TRANSPORTE
MATERIAL |  | UNIDAD | RENDIMIENTO | TARIFA | VR.UNITARIO
Transporte del robot y gripper (flete) |  | UNIDAD | 1 | $5000000 | $5000000.00
Trasiego de estructuras (banda, cercos) |  | UNIDAD | 1 | $1200000 | $1200000.00
Transporte interno a la planta |  | UNIDAD | 1 | $2000000.00 | $2000000.00
SUB-TOTAL |  |  |  |  | $8200000.00
4 - MANO DE OBRA
CUADRILLA |  | UNIDAD | RENDIMIENTO | VR. HH | VR. UNITARIO
Integrador robótico |  | UNIDAD | 40 | $200000 | $8000000.00
Técnico electromecánico |  | UNIDAD | 30 | $150000 | $4500000.00
Soldador (estructuras) |  | UNIDAD | 20 | $130000 | $2600000.00
Ayudante de montaje |  | UNIDAD | 20 | $100000 | $2000000.00
SUB-TOTAL |  |  |  |  | $17100000.00
5 - SUBCONTRATADO
CUADRILLA |  | UNIDAD | RENDIMIENTO | TARIFA | VR. UNITARIO
Programación avanzada PLC (S7) |  | UNIDAD | 1 | $4000000.00 | $4000000.00
Consultoría en seguridad (normas) |  | UNIDAD | 1 | $3000000.00 | $3000000.00
SUB-TOTAL |  |  |  |  | $7000000.00
6 - OTROS
ITEM |  | UNIDAD | RENDIMIENTO | TARIFA | VR. UNITARIO
Gastos varios (papelería, etc.) |  | UNIDAD | 1 | $1200000.00 | $1200000.00
Capacitación al personal |  | UNIDAD | 1 | $2500000.00 | $2500000.00
SUB-TOTAL |  |  |  |  | $3700000.00
TOTAL COSTO DIRECTO |  |  |  |  | $285949240.00

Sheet: APU-3
FORMATO DE APU
CONTRATISTA: | BRICAJO TOYS
NIT:
PROYECTO: | Automatizacion planta producción de juguetes
LOCALIZACIÓN: | Bogota - Colombia
ACTIVIDAD A COTIZAR: | Automatizacion planta producción de juguetes
ITEM | 3
DESCRIPCION DEL ITEM | Banda transportadora 1
UNIDAD | ML
1 - EQUIPO
DESCRIPCIÓN DETALLADA | MARCA | UNIDAD | RENDIMIENTO | TARIFA | VR. UNITARIO
Pulidora 4 1/2 pulgadas | DeWalt | UNIDAD | 0.7 | $4650 | $3255.00
Planta electrica | DeWalt | UNIDAD | 0.8 | $4650 | $3720.00
Pulidora 7" | DeWalt | UNIDAD | 0.8 | $4350 | $3480.00
Multimetro osciloscopio | Generico | UNIDAD | 1 | $15000 | $15000.00
Taladro rotomartillo | DeWalt | UNIDAD | 0.6 | $4200 | $2520.00
Equipo de soldadura SMAW | Generico | UNIDAD | 0.7 | $4650 | $3255.00
Compresor alta capacidad | DeWalt | UNIDAD | 0.7 | $3800 | $2660.00
Pistola de pintura | Corneta | UNIDAD | 0.5 | $2500 | $1250.00
kit tintas penetrantes | Magnaflux | UNIDAD | 0.8 | $1100 | $880.00
kit espesor de pinturas | Varios | UNIDAD | 0.8 | $500 | $400.00
SUB-TOTAL |  |  |  |  | $36420.00
2 - MATERIALES
DESCRIPCIÓN | MARCA | UNIDAD | CANTIDAD | PRECIO UNIT | VR. UNITARIO
Pintura blanca anticorrosiva espesor de película 4 mills | kollor | GALÓN | 0.35 | $75000 | $26250.00
Perfil funcional aluminio | mk gruop | ML | 0.35 | $85000 | $29750.00
Rodillo 2"x90cm | Indurob | UNIDAD | 3 | $75000 | $450000.00
Banda caucho 3 lonas 100cm ancho | Transmibandas | ML | 1 | $75000 | $75000.00
Chumacera tension SKF 1" | SKF | Unidad | 0.286 | $150000 | $42857.14
Tambor cabeza 2"x90cm | Indurob | Unidad | 0.1 | $350000 | $35000.00
Motor asincrono 5,5 Hp | WEG | Unidad | 0.1 | $1500000 | $30000.00
Variador de frecuencia 6 HP | Delta | Unidad | 0.1 | $980000 | $98000.00
Reductor sinfin corona | SEW | Unidad | 0.1 | $1250000 | $125000.00
Tablero control | Varios | Unidad | 0.1 | $1250000 | $125000.00
Cable UTP | varios | ML | 100 | $1700 | $170000.00
Cable control | varios | ML | 100 | $2500 | $250000.00
Perno anclaje 1/2" | Fixer | UNIDAD | 150 | $1350 | $202500.00
PC control | varios | UNIDAD | 0.05 | $3500000 | $175000.00
PLC comunicación S7--1200 | Siemens | UNIDAD | 0.05 | $1350000 | $67500.00
Brocas | Irwin | ML | 0.2 | $7000 | $1400.00
Disco de corte | DeWalt | UNIDAD | 0.45 | $9500 | $4275.00
Disco de desbaste | DeWalt | UNIDAD | 0.45 | $9500 | $4275.00
Disco Flap | DeWalt | UNIDAD | 0.45 | $26900 | $12105.00
Electrodo revestido | WestArco | kg | 0.2 | $21000 | $4200.00
Tubo cuadrado 50x50x2 | colmena | UNIDAD | 1 | $156000 | $156000.00
Angulo 1" x 3/16 | Colmena | UNIDAD | 0.8 | $45300 | $36240.00
Tornillo | Fixer | UNIDAD | 4 | $250 | $1000.00
Golpe dobles | varios | UNIDAD | 2 | $1500 | $3000.00
obra civil | Varios | Unidad | 2 | $15000 | $30000.00
Platinas | Varios | UNIDAD | 2 | $3500 | $7000.00
SUB-TOTAL |  |  |  |  | $2161352.14
3 - TRANSPORTE
MATERIAL |  | UNIDAD | RENDIMIENTO | TARIFA | VR.UNITARIO
Transporte estructuras |  | Unidad | 1 | $20000 | $20000.00
Trasiego material |  | UNIDAD | 1 | $1200 | $10000.00
SUB-TOTAL |  |  |  |  | $30000.00
4 - MANO DE OBRA
CUADRILLA |  | UNIDAD | RENDIMIENTO | VR. HH | VR. UNITARIO
Ayudante Soldadura |  | UNIDAD | 5 | $50000 | $250000.00
Ayudante Montaje |  | UNIDAD | 5 | $40000 | $200000.00
Tecnico electromecanico |  | UNIDAD | 5 | $60000 | $300000.00
SUB-TOTAL |  |  |  |  | $750000.00
5 - SUBCONTRATADO
CUADRILLA |  | UNIDAD | RENDIMIENTO | VR. HH | VR. UNITARIO
SUB-TOTAL |  |  |  |  | $ -
6 - OTROS
 |  | UNIDAD | RENDIMIENTO | VR. HH | VR. UNITARIO
SUB-TOTAL |  |  |  |  | $ -
TOTAL COSTO DIRECTO |  |  |  |  | $2977772.14

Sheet: APU-4
FORMATO DE APU
CONTRATISTA: | BRICAJO TOYS
NIT:
PROYECTO: | Automatizacion planta producción de juguetes
LOCALIZACIÓN: | Bogota - Colombia
ACTIVIDAD A COTIZAR: | Automatizacion planta producción de juguetes
ITEM | 4
DESCRIPCION DEL ITEM | Banda transportadora 2 y 3
UNIDAD | ML
1 - EQUIPO
DESCRIPCIÓN DETALLADA | MARCA | UNIDAD | RENDIMIENTO | TARIFA | VR. UNITARIO
Pulidora 4 1/2 pulgadas | DeWalt | UNIDAD | 0.7 | $4650 | $3255.00
Planta electrica | DeWalt | UNIDAD | 0.8 | $4650 | $3720.00
Pulidora 7" | DeWalt | UNIDAD | 0.8 | $4350 | $3480.00
Multimetro osciloscopio |  | UNIDAD | 1 | $15000 | $15000.00
Taladro rotomartillo | DeWalt | UNIDAD | 0.6 | $4200 | $2520.00
Equipo de soldadura SMAW | Generico | UNIDAD | 0.7 | $4650 | $3255.00
Compresor alta capacidad | DeWalt | UNIDAD | 0.7 | $3800 | $2660.00
Pistola de pintura | Corneta | UNIDAD | 0.5 | $2500 | $1250.00
kit tintas penetrantes | Magnaflux | UNIDAD | 0.8 | $1100 | $880.00
kit espesor de pinturas | Varios | UNIDAD | 0.8 | $500 | $400.00
SUB-TOTAL |  |  |  |  | $36420.00
2 - MATERIALES
DESCRIPCIÓN | MARCA | UNIDAD | CANTIDAD | PRECIO UNIT | VR. UNITARIO
Pintura blanca anticorrosiva espesor de película 4 mills | kollor | GALÓN | 0.35 | $75000 | $26250.00
Rodillo 2"x90cm | Indurob | UNIDAD | 3 | $75000 | $225000.00
Banda caucho 3 lonas 50cm ancho | Transmibandas | ML | 2 | $45000 | $90000.00
Perfil funcional aluminio | mk gruop | ML | 0.35 | $85000 | $29750.00
Chumacera tension SKF 1" | SKF | Unidad | 0.267 | $150000 | $40000.00
Tambor cabeza 2"x90cm | Indurob | Unidad | 0.2 | $350000 | $70000.00
Motor asincrono 5,5 Hp | WEG | Unidad | 0.2 | $1500000 | $30000.00
Variador de frecuencia 6 HP | Delta | Unidad | 0.2 | $980000 | $196000.00
Reductor sinfin corona | SEW | Unidad | 0.2 | $1250000 | $250000.00
Tablero control | Varios | Unidad | 0.2 | $1250000 | $250000.00
Cable UTP | varios | ML | 100 | $1700 | $170000.00
Cable control | varios | ML | 200 | $2500 | $500000.00
Perno anclaje 1/2" | Fixer | UNIDAD | 150 | $1350 | $202500.00
PC control | varios | UNIDAD | 0.05 | $3500000 | $175000.00
PLC comunicación S7 1200 | Siemens | UNIDAD | 0.05 | $1350000 | $67500.00
Brocas | Irwin | ML | 0.2 | $7000 | $1400.00
Disco de corte | DeWalt | UNIDAD | 0.45 | $9500 | $4275.00
Disco de desbaste | DeWalt | UNIDAD | 0.45 | $9500 | $4275.00
Disco Flap | DeWalt | UNIDAD | 0.45 | $26900 | $12105.00
Electrodo revestido | WestArco | kg | 0.2 | $21000 | $4200.00
Tubo cuadrado 50x50x2 | colmena | UNIDAD | 1 | $156000 | $156000.00
Angulo 1" x 3/16 | Colmena | UNIDAD | 0.8 | $45300 | $36240.00
Tornillo | Fixer | UNIDAD | 4 | $250 | $1000.00
Golpe dobles | varios | UNIDAD | 2 | $1500 | $3000.00
obra civil | Varios | Unidad | 2 | $15000 | $30000.00
Platinas | Varios | UNIDAD | 2 | $3500 | $7000.00
SUB-TOTAL |  |  |  |  | $2582895.00
3 - TRANSPORTE
MATERIAL |  | UNIDAD | RENDIMIENTO | TARIFA | VR.UNITARIO
Transporte estructuras |  | Unidad | 1 | $30000 | $30000.00
Trasiego material |  | UNIDAD | 1 | $5000 | $5000.00
SUB-TOTAL |  |  |  |  | $35000.00
4 - MANO DE OBRA
CUADRILLA |  | UNIDAD | RENDIMIENTO | VR. HH | VR. UNITARIO
Ayudante Montaje |  | UNIDAD | 2 | $40000 | $80000.00
Tecnico electromecanico |  | UNIDAD | 2 | $60000 | $120000.00
SUB-TOTAL |  |  |  |  | $200000.00
5 - SUBCONTRATADO
CUADRILLA |  | UNIDAD | RENDIMIENTO | VR. HH | VR. UNITARIO
SUB-TOTAL |  |  |  |  | $ -
6 - OTROS
 |  | UNIDAD | RENDIMIENTO | VR. HH | VR. UNITARIO
SUB-TOTAL |  |  |  |  | $ -
TOTAL COSTO DIRECTO |  |  |  |  | $2854315.00

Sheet: APU-5
FORMATO DE APU
CONTRATISTA: | BRICAJO TOYS
NIT:
PROYECTO: | Automatizacion planta producción de juguetes
LOCALIZACIÓN: | Bogota - Colombia
ACTIVIDAD A COTIZAR: | Automatizacion planta producción de juguetes
ITEM | 5
DESCRIPCION DEL ITEM | Banda transportadora 4
UNIDAD | ML
1 - EQUIPO
DESCRIPCIÓN DETALLADA | MARCA | UNIDAD | RENDIMIENTO | TARIFA | VR. UNITARIO
Pulidora 4 1/2 pulgadas | DeWalt | UNIDAD | 0.7 | $4650 | $3255.00
Planta electrica | DeWalt | UNIDAD | 0.8 | $4650 | $3720.00
Pulidora 7" | DeWalt | UNIDAD | 0.8 | $4350 | $3480.00
Multimetro osciloscopio | Generico | UNIDAD | 1 | $15000 | $15000.00
Taladro rotomartillo | DeWalt | UNIDAD | 0.6 | $4200 | $2520.00
Equipo de soldadura SMAW | Generico | UNIDAD | 0.7 | $4650 | $3255.00
Compresor alta capacidad | DeWalt | UNIDAD | 0.7 | $3800 | $2660.00
Pistola de pintura | Corneta | UNIDAD | 0.5 | $2500 | $1250.00
kit tintas penetrantes | Magnaflux | UNIDAD | 0.8 | $1100 | $880.00
kit espesor de pinturas | Varios | UNIDAD | 0.8 | $500 | $400.00
SUB-TOTAL |  |  |  |  | $36420.00
2 - MATERIALES
DESCRIPCIÓN | MARCA | UNIDAD | CANTIDAD | PRECIO UNIT | VR. UNITARIO
Pintura blanca anticorrosiva espesor de película 4 mills | kollor | GALÓN | 0.7 | $75000 | $52500.00
Perfil funcional aluminio | mk gruop | ML | 0.7 | $85000 | $59500.00
Rodillo 2"x90cm | Indurob | UNIDAD | 6 | $75000 | $450000.00
Banda caucho 3 lonas 100cm ancho | Transmibandas | ML | 3 | $75000 | $225000.00
Chumacera tension SKF 1" | SKF | Unidad | 0.286 | $150000 | $42857.14
Tambor cabeza 2"x90cm | Indurob | Unidad | 0.1 | $350000 | $35000.00
Motor asincrono 5,5 Hp | WEG | Unidad | 0.1 | $1500000 | $150000.00
Variador de frecuencia 6 HP | Delta | Unidad | 0.1 | $980000 | $98000.00
Reductor sinfin corona | SEW | Unidad | 0.1 | $1250000 | $125000.00
Tablero control | Varios | Unidad | 0.1 | $1250000 | $125000.00
Cable UTP | varios | ML | 100 | $1700 | $170000.00
Cable control | varios | ML | 100 | $2500 | $250000.00
Perno anclaje 1/2" | Fixer | UNIDAD | 150 | $1350 | $202500.00
PC control | varios | UNIDAD | 0.05 | $3500000 | $175000.00
PLC comunicación s7-1200 | Siemens | UNIDAD | 0.05 | $1350000 | $67500.00
Brocas | Irwin | ML | 0.2 | $7000 | $1400.00
Disco de corte | DeWalt | UNIDAD | 0.45 | $9500 | $4275.00
Disco de desbaste | DeWalt | UNIDAD | 0.45 | $9500 | $4275.00
Disco Flap | DeWalt | UNIDAD | 0.45 | $26900 | $12105.00
Electrodo revestido | WestArco | kg | 0.4 | $21000 | $8400.00
Tubo cuadrado 50x50x2 | colmena | UNIDAD | 2 | $156000 | $312000.00
Angulo 1" x 3/16 | Colmena | UNIDAD | 1.6 | $45300 | $72480.00
Tornillo | Fixer | UNIDAD | 8 | $250 | $2000.00
Golpe dobles | varios | UNIDAD | 4 | $1500 | $6000.00
obra civil | Varios | Unidad | 2 | $15000 | $30000.00
Platinas | Varios | UNIDAD | 4 | $3500 | $14000.00
SUB-TOTAL |  |  |  |  | $2694792.14
3 - TRANSPORTE
MATERIAL |  | UNIDAD | RENDIMIENTO | TARIFA | VR.UNITARIO
Transporte estructuras |  | Unidad | 1 | $20000 | $20000.00
Trasiego material |  | UNIDAD | 1 | $1200 | $10000.00
SUB-TOTAL |  |  |  |  | $30000.00
4 - MANO DE OBRA
CUADRILLA |  | UNIDAD | RENDIMIENTO | VR. HH | VR. UNITARIO
Ayudante Soldadura |  | UNIDAD | 5 | $50000 | $250000.00
Ayudante Montaje |  | UNIDAD | 5 | $40000 | $200000.00
Tecnico electromecanico |  | UNIDAD | 5 | $60000 | $300000.00
SUB-TOTAL |  |  |  |  | $750000.00
5 - SUBCONTRATADO
CUADRILLA |  | UNIDAD | RENDIMIENTO | VR. HH | VR. UNITARIO
SUB-TOTAL |  |  |  |  | $ -
6 - OTROS
 |  | UNIDAD | RENDIMIENTO | VR. HH | VR. UNITARIO
SUB-TOTAL |  |  |  |  | $ -
TOTAL COSTO DIRECTO |  |  |  |  | $3511212.14

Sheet: APU-6
FORMATO DE APU
CONTRATISTA: | BRICAJO TOYS
NIT:
PROYECTO: | Automatizacion planta producción de juguetes
LOCALIZACIÓN: | Bogota - Colombia
ACTIVIDAD A COTIZAR: | Automatizacion planta producción de juguetes
ITEM | 6
DESCRIPCION DEL ITEM | Banda transportadora 5
UNIDAD | ML
1 - EQUIPO
DESCRIPCIÓN DETALLADA | MARCA | UNIDAD | RENDIMIENTO | TARIFA | VR. UNITARIO
Pulidora 4 1/2 pulgadas | DeWalt | UNIDAD | 0.7 | $4650 | $3255.00
Planta electrica | DeWalt | UNIDAD | 0.8 | $4650 | $3720.00
Pulidora 7" | DeWalt | UNIDAD | 0.8 | $4350 | $3480.00
Multimetro osciloscopio |  | UNIDAD | 1 | $15000 | $15000.00
Taladro rotomartillo | DeWalt | UNIDAD | 0.6 | $4200 | $2520.00
Equipo de soldadura SMAW | Generico | UNIDAD | 0.7 | $4650 | $3255.00
Compresor alta capacidad | DeWalt | UNIDAD | 0.7 | $3800 | $2660.00
Pistola de pintura | Corneta | UNIDAD | 0.5 | $2500 | $1250.00
kit tintas penetrantes | Magnaflux | UNIDAD | 0.8 | $1100 | $880.00
kit espesor de pinturas | Varios | UNIDAD | 0.8 | $500 | $400.00
SUB-TOTAL |  |  |  |  | $36420.00
2 - MATERIALES
DESCRIPCIÓN | MARCA | UNIDAD | CANTIDAD | PRECIO UNIT | VR. UNITARIO
Pintura blanca anticorrosiva espesor de película 4 mills | kollor | GALÓN | 0.35 | $75000 | $26250.00
Rodillo 2"x90cm | Indurob | UNIDAD | 3 | $75000 | $225000.00
Banda caucho 3 lonas 50cm ancho | Transmibandas | ML | 1 | $45000 | $45000.00
Perfil funcional aluminio | mk gruop | ML | 0.35 | $85000 | $29750.00
Chumacera tension SKF 1" | SKF | Unidad | 0.267 | $150000 | $40000.00
Tambor cabeza 2"x90cm | Indurob | Unidad | 0.1 | $350000 | $35000.00
Motor asincrono 5,5 Hp | WEG | Unidad | 0.1 | $1500000 | $150000.00
Variador de frecuencia 6 HP | Delta | Unidad | 0.1 | $980000 | $98000.00
Reductor sinfin corona | SEW | Unidad | 0.1 | $1250000 | $125000.00
Tablero control | Varios | Unidad | 0.1 | $1250000 | $125000.00
Cable UTP | varios | ML | 100 | $1700 | $170000.00
Cable control | varios | ML | 200 | $2500 | $500000.00
Perno anclaje 1/2" | Fixer | UNIDAD | 150 | $1350 | $202500.00
PC control | varios | UNIDAD | 0.05 | $3500000 | $175000.00
PLC comunicación S7-1200 | Siemens | UNIDAD | 0.05 | $1350000 | $67500.00
Brocas | Irwin | ML | 0.2 | $7000 | $1400.00
Disco de corte | DeWalt | UNIDAD | 0.45 | $9500 | $4275.00
Disco de desbaste | DeWalt | UNIDAD | 0.45 | $9500 | $4275.00
Disco Flap | DeWalt | UNIDAD | 0.45 | $26900 | $12105.00
Electrodo revestido | WestArco | kg | 0.2 | $21000 | $4200.00
Tubo cuadrado 50x50x2 | colmena | UNIDAD | 1 | $156000 | $156000.00
Angulo 1" x 3/16 | Colmena | UNIDAD | 0.8 | $45300 | $36240.00
Tornillo | Fixer | UNIDAD | 4 | $250 | $1000.00
Golpe dobles | varios | UNIDAD | 2 | $1500 | $3000.00
obra civil | Varios | Unidad | 2 | $15000 | $30000.00
Platinas | Varios | UNIDAD | 2 | $3500 | $7000.00
SUB-TOTAL |  |  |  |  | $2274895.00
3 - TRANSPORTE
MATERIAL |  | UNIDAD | RENDIMIENTO | TARIFA | VR.UNITARIO
Transporte estructuras |  | Unidad | 1 | $30000 | $30000.00
Trasiego material |  | UNIDAD | 1 | $5000 | $5000.00
SUB-TOTAL |  |  |  |  | $35000.00
4 - MANO DE OBRA
CUADRILLA |  | UNIDAD | RENDIMIENTO | VR. HH | VR. UNITARIO
Ayudante Montaje |  | UNIDAD | 2.5 | $40000 | $100000.00
Tecnico electromecanico |  | UNIDAD | 2.5 | $60000 | $150000.00
SUB-TOTAL |  |  |  |  | $250000.00
5 - SUBCONTRATADO
CUADRILLA |  | UNIDAD | RENDIMIENTO | VR. HH | VR. UNITARIO
SUB-TOTAL |  |  |  |  | $ -
6 - OTROS
 |  | UNIDAD | RENDIMIENTO | VR. HH | VR. UNITARIO
SUB-TOTAL |  |  |  |  | $ -
TOTAL COSTO DIRECTO |  |  |  |  | $2596315.00

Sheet: APU-7
FORMATO DE APU
CONTRATISTA: | BRICAJO TOYS
NIT:
PROYECTO: | Automatizacion planta producción de juguetes
LOCALIZACIÓN: | Bogota - Colombia
ACTIVIDAD A COTIZAR: | Automatizacion planta producción de juguetes
ITEM | 7
DESCRIPCION DEL ITEM | Banda transportadora 6
UNIDAD | ML
1 - EQUIPO
DESCRIPCIÓN DETALLADA | MARCA | UNIDAD | RENDIMIENTO | TARIFA | VR. UNITARIO
Pulidora 4 1/2 pulgadas | DeWalt | UNIDAD | 0.7 | $4650 | $3255.00
Planta electrica | DeWalt | UNIDAD | 0.8 | $4650 | $3720.00
Pulidora 7" | DeWalt | UNIDAD | 0.8 | $4350 | $3480.00
Multimetro osciloscopio |  | UNIDAD | 1 | $15000 | $15000.00
Taladro rotomartillo | DeWalt | UNIDAD | 0.6 | $4200 | $2520.00
Equipo de soldadura SMAW | Generico | UNIDAD | 0.7 | $4650 | $3255.00
Compresor alta capacidad | DeWalt | UNIDAD | 0.7 | $3800 | $2660.00
Pistola de pintura | Corneta | UNIDAD | 0.5 | $2500 | $1250.00
kit tintas penetrantes | Magnaflux | UNIDAD | 0.8 | $1100 | $880.00
kit espesor de pinturas | Varios | UNIDAD | 0.8 | $500 | $400.00
SUB-TOTAL |  |  |  |  | $36420.00
2 - MATERIALES
DESCRIPCIÓN | MARCA | UNIDAD | CANTIDAD | PRECIO UNIT | VR. UNITARIO
Pintura blanca anticorrosiva espesor de película 4 mills | kollor | GALÓN | 0.35 | $75000 | $26250.00
Rodillo 2"x90cm | Indurob | UNIDAD | 4 | $75000 | $300000.00
Banda caucho 3 lonas 50cm ancho | Transmibandas | ML | 1 | $45000 | $45000.00
Perfil funcional aluminio | mk gruop | ML | 0.35 | $85000 | $29750.00
Chumacera tension SKF 1" | SKF | Unidad | 0.267 | $150000 | $40000.00
Tambor cabeza 2"x90cm | Indurob | Unidad | 0.1 | $350000 | $35000.00
Motor asincrono 5,5 Hp | WEG | Unidad | 0.1 | $1500000 | $150000.00
Variador de frecuencia 6 HP | Delta | Unidad | 0.1 | $980000 | $98000.00
Reductor sinfin corona | SEW | Unidad | 0.1 | $1250000 | $125000.00
Tablero control | Varios | Unidad | 0.1 | $1250000 | $125000.00
Cable UTP | varios | ML | 100 | $1700 | $170000.00
Cable control | varios | ML | 200 | $2500 | $500000.00
Perno anclaje 1/2" | Fixer | UNIDAD | 150 | $1350 | $202500.00
PC control | varios | UNIDAD | 0.05 | $3500000 | $175000.00
PLC comunicación S7 1200 | Siemens | UNIDAD | 0.05 | $1350000 | $67500.00
Brocas | Irwin | ML | 0.2 | $7000 | $1400.00
Disco de corte | DeWalt | UNIDAD | 0.45 | $9500 | $4275.00
Disco de desbaste | DeWalt | UNIDAD | 0.45 | $9500 | $4275.00
Disco Flap | DeWalt | UNIDAD | 0.45 | $26900 | $12105.00
Electrodo revestido | WestArco | kg | 0.2 | $21000 | $4200.00
Tubo cuadrado 50x50x2 | colmena | UNIDAD | 1 | $156000 | $156000.00
Angulo 1" x 3/16 | Colmena | UNIDAD | 0.8 | $45300 | $36240.00
Tornillo | Fixer | UNIDAD | 4 | $250 | $1000.00
Golpe dobles | varios | UNIDAD | 2 | $1500 | $3000.00
obra civil | Varios | Unidad | 2 | $15000 | $30000.00
Platinas | Varios | UNIDAD | 2 | $3500 | $7000.00
SUB-TOTAL |  |  |  |  | $2349895.00
3 - TRANSPORTE
MATERIAL |  | UNIDAD | RENDIMIENTO | TARIFA | VR.UNITARIO
Transporte estructuras |  | Unidad | 1 | $30000 | $30000.00
Trasiego material |  | UNIDAD | 1 | $5000 | $5000.00
SUB-TOTAL |  |  |  |  | $35000.00
4 - MANO DE OBRA
CUADRILLA |  | UNIDAD | RENDIMIENTO | VR. HH | VR. UNITARIO
Ayudante Montaje |  | UNIDAD | 2 | $40000 | $80000.00
Tecnico electromecanico |  | UNIDAD | 2 | $60000 | $120000.00
SUB-TOTAL |  |  |  |  | $200000.00
5 - SUBCONTRATADO
CUADRILLA |  | UNIDAD | RENDIMIENTO | VR. HH | VR. UNITARIO
SUB-TOTAL |  |  |  |  | $ -
6 - OTROS
 |  | UNIDAD | RENDIMIENTO | VR. HH | VR. UNITARIO
SUB-TOTAL |  |  |  |  | $ -
TOTAL COSTO DIRECTO |  |  |  |  | $2621315.00
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

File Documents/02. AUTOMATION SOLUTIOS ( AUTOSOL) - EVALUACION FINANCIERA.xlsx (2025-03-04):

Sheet: Proyección ventas
Estimación ventas mensuales por tipo de juguete (Millones COP)
Mes | Moto | Barco | Casa |  |  | Precio(COP) | Ventas Mensual | Producción máxima (unidades) por turno | Producción máxima (Unidades) al día | Turnos por día | Distribución Mensual de ventas estimada:
Enero | 292.57 | 256.00 | 182.86 |  | Motos | $10000.00 | 40% | 16960 | 33920 | 2 | Diciembre | 30%
Febrero | 292.57 | 256.00 | 182.86 |  | Barcos | $12000.00 | 35% | 14790 | 29580 |  | Abril | 12%
Marzo | 292.57 | 256.00 | 182.86 |  | Casas | $15000.00 | 25% | 10440 | 20880 |  | Junio - Julio | 10%
Abril | 819.20 | 716.80 | 512.00 |  |  |  |  |  |  |  | Octubre | 8%
Mayo | 292.57 | 256.00 | 182.86 |  |  |  |  |  |  |  | Demás meses (7) | 4.3
Junio | 682.67 | 597.33 | 426.67
Julio | 682.67 | 597.33 | 426.67
Agosto | 292.57 | 256.00 | 182.86
Septiembre | 292.57 | 256.00 | 182.86
Octubre | 546.13 | 477.87 | 341.33
Noviembre | 292.57 | 256.00 | 182.86
Diciembre | 2048.00 | 1792.00 | 1280.00 |  | Estimación ventas anuales totales (Millones COP)
 |  |  |  |  | 17066.66667
Estimación ventas mensuales por tipo de juguete (Unidades) |  |  |  |  | Estimación ventas de planta automatizada (Millones COP)
Mes | Moto | Barco | Casa |  | 8533.333333
Enero | 29257.14286 | 21333.33333 | 12190.47619
Febrero | 29257.14286 | 21333.33333 | 12190.47619 |  | Porcentaje de mercado abarcado
Marzo | 29257.14286 | 21333.33333 | 12190.47619 |  | 50%
Abril | 81920 | 59733.33333 | 34133.33333
Mayo | 29257.14286 | 21333.33333 | 12190.47619
Junio | 68266.66667 | 49777.77778 | 28444.44444
Julio | 68266.66667 | 49777.77778 | 28444.44444
Agosto | 29257.14286 | 21333.33333 | 12190.47619
Septiembre | 29257.14286 | 21333.33333 | 12190.47619
Octubre | 54613.33333 | 39822.22222 | 22755.55556
Noviembre | 29257.14286 | 21333.33333 | 12190.47619
Diciembre | 204800 | 149333.3333 | 85333.33333
Producción proyectada mensual por tipo de juguete (Unidades) |  |  |  | Producción proyectada mensual por tipo de juguete dada la producción máxima de la planta automatizada (Unidades)
Mes | Moto | Barco | Casa | Mes | Moto | Barco | Casa
Enero | 14628.57143 | 10666.66667 | 6095.238095 | Enero | 14628.57143 | 10666.66667 | 6095.238095
Febrero | 14628.57143 | 10666.66667 | 6095.238095 | Febrero | 14628.57143 | 10666.66667 | 6095.238095
Marzo | 14628.57143 | 10666.66667 | 6095.238095 | Marzo | 21668.57143 | 10666.66667 | 6095.238095
Abril | 40960 | 29866.66667 | 17066.66667 | Abril | 33920 | 29866.66667 | 17066.66667
Mayo | 14628.57143 | 10666.66667 | 6095.238095 | Mayo | 14628.57143 | 10666.66667 | 6095.238095
Junio | 34133.33333 | 24888.88889 | 14222.22222 | Junio | 34133.33333 | 24888.88889 | 14222.22222
Julio | 34133.33333 | 24888.88889 | 14222.22222 | Julio | 34133.33333 | 24888.88889 | 14222.22222
Agosto | 14628.57143 | 10666.66667 | 6095.238095 | Agosto | 37912.38095 | 10666.66667 | 6095.238095
Septiembre | 14628.57143 | 10666.66667 | 6095.238095 | Septiembre | 33920 | 27171.11111 | 6095.238095
Octubre | 27306.66667 | 19911.11111 | 11377.77778 | Octubre | 33920 | 29580 | 18379.68254
Noviembre | 14628.57143 | 10666.66667 | 6095.238095 | Noviembre | 33920 | 29580 | 20880
Diciembre | 102400 | 74666.66667 | 42666.66667 | Diciembre | 33920 | 29580 | 20880
Producción proyectada mensual por tipo de juguete dada la producción máxima de la planta automatizada (Millones COP)
Mes | Moto | Barco | Casa
Enero | 146.2857143 | 128 | 91.42857143
Febrero | 146.2857143 | 128 | 91.42857143
Marzo | 146.2857143 | 128 | 91.42857143
Abril | 409.6 | 358.4 | 256
Mayo | 146.2857143 | 128 | 91.42857143
Junio | 341.3333333 | 298.6666667 | 213.3333333
Julio | 341.3333333 | 298.6666667 | 213.3333333
Agosto | 146.2857143 | 128 | 91.42857143
Septiembre | 146.2857143 | 128 | 91.42857143
Octubre | 273.0666667 | 238.9333333 | 170.6666667
Noviembre | 146.2857143 | 128 | 91.42857143
Diciembre | 1024 | 896 | 640

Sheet: Evaluación financiera
AUTOMATION SOLUTIOS ( AUSOL) - EVALUACION FINANCIERA
Proyección ventas anual | 8533333333 |  | 4.3% | 4.3% | 4.3% | 12% | 4.3% | 10% | 10% | 4.3% | 4.3% | 8% | 4.3% | 30%
PRODUCTO | Cant. Unidades | Participación | Enero | Febrero | Marzo | Abril | Mayo | Junio | Julio | Agosto | Septiembre | Octubre | Noviembre | Diciembre
Barco | 248888.89 | 35% | 128426666.7 | 128426666.7 | 128426666.7 | 358400000 | 128426666.7 | 298666666.7 | 298666666.7 | 128426666.7 | 128426666.7 | 238933333.3 | 128426666.7 | 896000000
Casa | 568888.89 | 25% | 91733333.33 | 91733333.33 | 91733333.33 | 256000000 | 91733333.33 | 213333333.3 | 213333333.3 | 91733333.33 | 91733333.33 | 170666666.7 | 91733333.33 | 640000000
Moto | 341333.33 | 40% | 146773333.3 | 146773333.3 | 146773333.3 | 409600000 | 146773333.3 | 341333333.3 | 341333333.3 | 146773333.3 | 146773333.3 | 273066666.7 | 146773333.3 | 1024000000
TOTAL VENTAS | 1159111.111 |  | 366933333.3 | 366933333.3 | 366933333.3 | 1024000000 | 366933333.3 | 853333333.3 | 853333333.3 | 366933333.3 | 366933333.3 | 682666666.7 | 366933333.3 | 2560000000
COSTOS (Variables)
Materia prima,empaque |  | 15% | 55040000 | 55040000 | 55040000 | 153600000 | 55040000 | 128000000 | 128000000 | 55040000 | 55040000 | 102400000 | 55040000 | 384000000
Energía eléctrica |  | 3% | 11008000 | 11008000 | 11008000 | 30720000 | 11008000 | 25600000 | 25600000 | 11008000 | 11008000 | 20480000 | 11008000 | 76800000
GASTOS (Fijos)
Administracion y Operarios |  | 32800000 | 32800000 | 32800000 | 32800000 | 32800000 | 32800000 | 32800000 | 32800000 | 32800000 | 32800000 | 32800000 | 32800000 | 32800000
Bodega, Mantenimientos |  | 5000000 | 5000000 | 5000000 | 5000000 | 5000000 | 5000000 | 5000000 | 5000000 | 5000000 | 5000000 | 5000000 | 5000000 | 5000000
UAI (Antes de Impuestos) |  |  | 263085333.3 | 263085333.3 | 263085333.3 | 801880000 | 263085333.3 | 661933333.3 | 661933333.3 | 263085333.3 | 263085333.3 | 521986666.7 | 263085333.3 | 2061400000
IMPUESTOS (Tx)
Renta |  | 35% | 92079866.67 | 92079866.67 | 92079866.67 | 280658000 | 92079866.67 | 231676666.7 | 231676666.7 | 92079866.67 | 92079866.67 | 182695333.3 | 92079866.67 | 721490000
FLUJO DE CAJA |  | -967883006.3 | 171005466.7 | 171005466.7 | 171005466.7 | 521222000 | 171005466.7 | 430256666.7 | 430256666.7 | 171005466.7 | 171005466.7 | 339291333.3 | 171005466.7 | 1339910000
INVERSION EN MAQUINARIA | -951883006.3
INVERSION EN INGENIERÍA AUTOMATIZACIÓN | -16000000
VP | $2935693422
VPN | $1967810416
TIR | 25.8%
TIO | 5.0%
 | Todo el estudio se hace acuerdo al perfil de consumo y a la producción máximo de la compañía

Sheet: Justificación Costos
Costo materia prima y empaque |  |  |  |  |  | Bodega y Mantenimientos |  | $5000000.00
Costos promedio para fabricación de un juguete | $1854.00 | Costo promedio de los juguetes | $12333.33 | Porcentaje de materia prima y empaque respecto al costo de venta promedio del juguete | 15.03243243 | Bodega de 300 m cuadrados en zona industrial de bogotá | $4000000.00
Plástico de inyección | $750.00 |  |  |  |  | Mantenimiento mensual estimado | $1000000.00
Bolsa de empaque | $100.00
Caja de empaque | $4.00
Pintura | $1000.00
Energía eléctrica
Gasto promedio de energía por fabricación de juguete | 370.0301 | Costo kV/h para industria en Bogotá | 305.81 | Porcentaje de gasto de energía eléctrica respecto al costo promedio de venta del juguete | 3.000244054

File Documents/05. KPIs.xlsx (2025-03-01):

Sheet: Tiempos
Estaciones
N° | Etapa | Proceso (s) | Set-up (s) | Total | No es posible encontrar la relación real entre las inyectoras y los moldes de manera directa. Entonces, se parte de los resultados de Tecnomatix, para la obtención de esos tiempos, partiendo de un la suma los productos sobre el tiempo requerido para su producción
1.1 | Inyección negro | 16 | 24.17 | 40.17
1.2 | Inyección rojo | 16 | 24.17 | 40.17
1.3 | Inyección azul | 16 | 24.17 | 40.17
2 | Separación | 5 | 1 | 6
3 | Acabados | 3 | 1 | 4
3.1 | Ensamble paredes | 10 | 0 | 10
3.2 | Ensamble timon | 2.5 | 0 | 2.5
4.1 | Ensamble moto | 2 | 1 | 3
4.2 | Ensamble barco | 2.5 | 1 | 3.5
4.3 | Ensamble casa | 2 | 1 | 3
6 | Tampografía | 10 | 1 | 11
5 | Control de calidad | 5 | 1 | 6
7 | Empaquetado | 4 | 2 | 6
8 | Palletizado | 1.5 | 0.8 | 2.3
9 | Despacho | 30 | 10 | 40
 |  |  | Total | 217.81
Transporte
N° | Ubicación | Tiempo | Descripción detallada
1.1 | 1 a 2 | 4 | Negro y rojo a separación
1.2 | 1 a 2 | 14 | Azul a separación
2.1 | 2 a 3 | 20 | Negro y rojo a acabados
2.2 | 2 a 3 | 10 | Azul a acabados
3.1 | 3 a 4 | 16 | Acabos a buffer
3.2 | 3 a 4 | 16 | Paredes y timon buffers
4 | 4 a 5 | 2 | Buffers a bufferAssembler
5 | 5 a 6 | 15 | Assembler a tampografía
6 | 6 a 7 | 10 | Tampografía a calidad
7 | 7 a 8 | 4 | Calidad a empaquetado
8 | 8 a 9 | 2 | Empaquetado a caja
9 | 8 a 9 | 14 | Empaquetado a robot
10 | 9 a 10 | 10 | Robot a despacho
 | Total | 137

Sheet: VSM
Piezas moto | Cantidad | Por tanda |  | Juguete | Cantidad por tanda | Transporte | Tiempo medio (s) | Tiempo total por tanda (s) | Por día (h)
Rueda | 4 | 32 |  | Moto | 8 | Inyectora a separación | 9 | 27 | 0.84
Chasis | 1 | 8 |  | Barco | 7 | Separación a acabados | 15 | 36.75 | 1.14
Piezas Barco | Cantidad | Por tanda |  | Casa | 5 | Acabados a ensamble | 11.33333333 | 27.76666667 | 0.86
Timon 1 | 1 | 7 |  | Total | 20 | Ensamble a pintura | 15 | 15 | 0.47
Timon 2 | 1 | 7 |  |  |  | Pintura a calidad | 10 | 10 | 0.31
Superior | 1 | 7 |  | Moldes por tanda | 3 | Calidad a empaquetado | 4 | 80 | 2.49
Inferior | 1 | 7 |  |  |  | Cajas a robot | 14 | 11.2 | 0.35
Piezas Casa | Cantidad | Por tanda |  | Juguetes por caja | 25 | Robot a despacho | 10 | 44.8 | 1.39
Paredes | 4 | 20 |  | Cajas por pallet | 20 |  | Total (s) | 252.5166667
Puerta | 1 | 5 |  | Total cajas (día) | 89.6 |  |  | Total (h) | 7.856074074
Techo | 1 | 5 |  | Total pallets (día) | 4.48
 | Total | 98 |  |  |  | Juguete | Peso (kg) | Tanda | Día | Semana
 |  |  |  |  |  | Moto | 0.155 | 1.24 | 138.88 | 694.4
N° | Proceso | Tp (s) | Día (h) | Relación valor | 80.72% | Barco | 0.115 | 0.805 | 90.16 | 450.8
1 | Inyección | 120.51 | 3.75 | Relación transporte | 19.28% | Casa | 0.512 | 2.56 | 286.72 | 1433.6
2 | Separar | 18 | 0.56 | Total tiempo | 1309.80 |  |  |  | 515.76 | 2578.8
3 | Acabado | 392 | 12.20
4 | Ensamble | 63.33333333 | 1.97 | Los tiempos en el VSM son por tanda… Ya que es una tarea dispendiosa, hacerlo por unidad |  | Material | Día | Semana | Mes
5 | Tampografía | 220 | 6.84 |  |  | Cajas | 89.6 | 448 | 1792
6 | Calidad | 120 | 3.73 |  |  | Pintura (ml) | 11200 | 56000 | 224000
7 | Empaquetado | 120 | 3.73
8 | Paletizado | 1.84 | 0.06 |  |  | ml por juguete | 5
9 | Despacho | 1.6 | 0.05
 | Total (s) | 1057.283333
 |  | Total (h) | 32.89

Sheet: P. Rendimiento
Tandas por día (tandas/dia) | 112 | Jornada (h) | Unidades por tanda |  | Unidades por dia | Un por lote | Tandas por lote
Dias de turnos (turnos/lote) | 5 | 8.00 | Motos | 8 | 896 | 4480 | 560
Lote en tandas (tandas/lote) | 560 | Valor en pelletSource | Barcos | 7 | 784 | 3920 |  | 0.9466071429
 |  | 336 | Casas | 5 | 560 | 2800
Tandas reales (tandas/dia) | 115.36 | 346.08 |  | Unidades por dia | 2240 | 11200 | Q(un/lote)
 |  |  |  |  | Mensual | 44800
Indicadores | Valor |  |  | PC | 11200 |  | U | 100.000%
Tsu (min/lote) | 0.00 | Se asume un suministro constante |  | n | 1
Tc (min/un) | 0.21 | Turnos |  | S | 5
Tb (min/lote) | 2400.00 | 5.0 |  | H | 8
Tp (min/un) | 0.21
Rp (un/hora) | 280 |  |  |  |  |  | Salida de producto real
 |  |  |  |  |  |  | Juguete | Salida semanal (Max) | Salida mensual (Max)
 |  |  |  |  |  |  | Motos | 4134 | 16960 | 40.19909931%
 |  |  |  |  |  |  | Barcos | 3606 | 14790 | 35.0557004%
 |  |  |  |  |  |  | Casas | 2544 | 10440 | 24.74520028%
 |  |  |  | Takt (s) | 12.86 |  | Total | 10284 | 42190
 |  |  |  |  |  |  | % de error | 8.18% | 5.83%
MLT (min) | 10080 | 7.00
Tno (min) | 7680 | Tiempo entre turnos
 |  |  |  |  |  |  | Defectuosos | 318
 |  |  |  |  |  |  | Total | 10602

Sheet: E.G. Equipamiento
Disponibilidad por estación
Indicadores | Inyección | Separado | Acabado | Ensamble general | Tampografía | Calidad | Empaquetado | Palletizado | Despacho
MTBF (UT) (h) | 272 | 136 | 136 | 272 | 272 | 136 | 272 | 272 | 136
MTTM (DT) (h) | 6 | 1 | 1 | 3 | 3 | 1 | 3 | 6 | 1
A | 97.84% | 99.27% | 99.27% | 98.91% | 98.91% | 99.27% | 98.91% | 97.84% | 99.27%
OEE | 75.13%
A | 80.72% | PE | 95.95% |  |  |  |  | Se asume un 10% de desfase en el Tiempo de ciclo real, respecto al calculado
TER (h) | 6.46 | RE | 105.54%
TEP (h) | 8 | SE | 90.91%
TINP (h) | 1.54 | Q | 97.00%
TIP (h) | 0.00

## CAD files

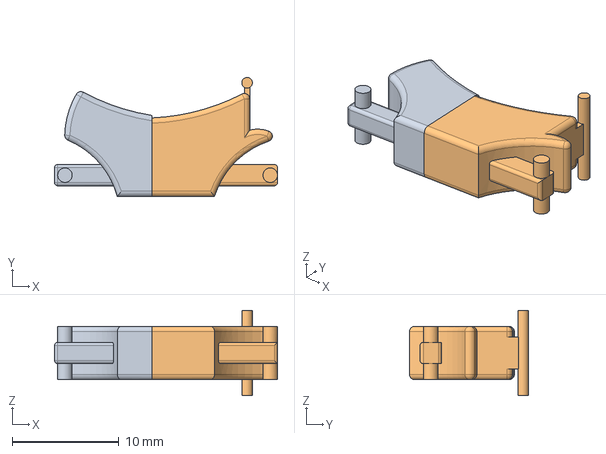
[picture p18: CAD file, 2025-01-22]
Design and simulation/Inventor/Modelado juguetes/Moto/Ensamblaje1.stp
20.9 x 11.2 x 8.00 mm
Moto
Moto_1

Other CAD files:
Design and simulation/Inventor/InjectionSetUp_RoboticCell/AssemblyAnalysis.iam
Design and simulation/Inventor/InjectionSetUp_RoboticCell/BaseMoldL.ipt
Design and simulation/Inventor/InjectionSetUp_RoboticCell/BaseMoldR_1.ipt
Design and simulation/Inventor/InjectionSetUp_RoboticCell/BaseMoldR_2.ipt
Design and simulation/Inventor/InjectionSetUp_RoboticCell/ControlPanel.ipt
Design and simulation/Inventor/InjectionSetUp_RoboticCell/EndEffector.ipt
Design and simulation/Inventor/InjectionSetUp_RoboticCell/FirstConveyor.ipt
Design and simulation/Inventor/InjectionSetUp_RoboticCell/InjectionMachine.ipt
Design and simulation/Inventor/InjectionSetUp_RoboticCell/Mold.ipt
Design and simulation/Inventor/InjectionSetUp_RoboticCell/MoldStore.ipt
Design and simulation/Inventor/InjectionSetUp_RoboticCell/OldVersions/AssemblyAnalysis.0017.iam
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

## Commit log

2025-01-16 Corrección bandas
    [Draft.ipt]
2025-01-17 Ultima corrección, bandas transportadoras
    [Draft.0001.ipt, Draft.ipt]
2025-01-17 Inicial files tecnomatix
    [Draft.0001.ipt, Draft.ipt]
2025-01-19 diseños
    [CasaJugueteAPM.iam, CasaJugueteAPM.ipt, EnsamblajeBarco.iam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]
2025-01-19 Piezas modificas para ensamble a presión y moto apta para molde
    [CasaJugueteAPM - copia.0007.ipt, CasaJugueteAPM.iam, CasaJugueteAPM.ipt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]
2025-01-20 Correcion grafico de planta
2025-01-20 Correciones en clase
    Asumir todo a criterio de investigación
2025-01-21 ToyPlant1.0
    Primer avance de la planta en tecnomatix
2025-01-21 Push para hacer pull de imagenes
    [Draft.0001.ipt, Draft.ipt]
2025-01-21 Adelanto de página web
2025-01-22 Foto para pag. web.
2025-01-22 Modelado actualizacion
    [Ensamblaje1.0001.iam, Ensamblaje1.0002.ipt, Ensamblaje1.iam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]
2025-01-22 Create AUTOMATION SOLUTIOS ( AUTOSOL) - EVALUACION FINANCIERA.xlsx
    Evaluación financiera
    [AUTOMATION SOLUTIOS ( AUTOSOL) - EVALUACION FINANCIERA.xlsx]
2025-01-23 Correción de planta e indicadores
    [02. AUTOMATION SOLUTIOS ( AUTOSOL) - EVALUACION FINANCIERA.xlsx]
2025-01-24 Correcciones digital factory
    TECNOMATIX
    VSM
    KPIs
    [03. KPIs.xlsx]
2025-01-29 Medidas reales
    [MedidaRealEnsamblajeCasa.ipt]
2025-02-02 Avance celda 1
    Cads y Robostudio
    [03. KPIs.xlsx, AssemblyAnalysis.iam, BaseMolde.0005.ipt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]
2025-02-11 VSM, Tecnomatix final y celda 1
    [03. KPIs.xlsx, EIO.cfg, MoldsStore.0001.ipt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]
2025-02-11 KPIS sem y mensual entorno real
    jhhj
    [03. KPIs.xlsx]
2025-02-11 Tecnomatix terminado
    Faltan los tiempos y materiales en el VSM
    [03. KPIs.xlsx]
2025-02-14 Juguetes definitivos
    Ensambles completados con medidas definitivas
    [EnsamblajeMoto.0002.iam, EnsamblajeMoto.0003.iam, EnsamblajeMoto.iam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]
2025-02-17 Proyección de ventas y perfil de demanda juguetes
    Excel y documento descriptivo con referencias
    [02. AUTOMATION SOLUTIOS ( AUTOSOL) - EVALUACION FINANCIERA.xlsx, 03. KPIs.xlsx]
2025-02-18 correciones evaluación financiera
    correciones evaluación financiera
    [02. AUTOMATION SOLUTIOS ( AUTOSOL) - EVALUACION FINANCIERA.xlsx]
2025-02-18 Después de reunión
    Después de reunión
    [02. AUTOMATION SOLUTIOS ( AUTOSOL) - EVALUACION FINANCIERA.xlsx]
2025-02-21 Celda Robotizada #1
    Celda 1 y VSM terminados
    [02. AUTOMATION SOLUTIOS ( AUTOSOL) - EVALUACION FINANCIERA.xlsx, 03. KPIs.xlsx, AssemblyAnalysis.0008.iam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]
2025-02-25 Celda robotizada #1
    Celda robotizada terminada 100% y correciones finales del VSM
    [03. KPIs.xlsx, AssemblyAnalysis.0008.iam, AssemblyAnalysis.0017.iam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]
2025-02-26 Parametrización de Evaluación financiera y proyección de ventas
    Parametrización de Evaluación financiera y proyección de ventas.
    [02. AUTOMATION SOLUTIOS ( AUTOSOL) - EVALUACION FINANCIERA.xlsx]
2025-03-01 NX y STUDIO5000
    [03. KPIs.xlsx, Assembler.0008.ipt, Assembler.0014.ipt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]
2025-03-03 cambios
    cambios
    [02. AUTOMATION SOLUTIOS ( AUTOSOL) - EVALUACION FINANCIERA.xlsx, BarcoFinal.0001.iam, BarcoFinal.iam]
2025-03-04 Update 02. AUTOMATION SOLUTIOS ( AUTOSOL) - EVALUACION FINANCIERA.xlsx
    [02. AUTOMATION SOLUTIOS ( AUTOSOL) - EVALUACION FINANCIERA.xlsx]
2025-03-05 LastCommit
    Ultimo Commit AUSOL 2024-2S
    [04. APUs.xlsx, ToyPlant.prt]
